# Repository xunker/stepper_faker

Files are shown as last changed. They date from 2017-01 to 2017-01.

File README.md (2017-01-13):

Stepper-Faker
=============

Arduino-based converter that lets unipolar steppers (e.g. 28BYJ-48 w/ ULN2003A)
pretend to be bipolar steppers for things like GRBL or Marlin. Built to work
with any Arduino-compatible atmega168/atmega328 board (ex: Arduino Uno or
Adafruit Pro Trinket). Also includes schematic for a custom carrier board that
makes connecting the steppers a snap!

Provides interface pins that work the same as the
[EasyDriver](http://www.schmalzhaus.com/EasyDriver/)
or [DRV8825/A4988 StepStick](https://www.pololu.com/product/1182) and can be
directly connected to a micro-controller running GRBL using the
[standard wiring](https://github.com/gnea/grbl/wiki/Connecting-Grbl).

Up to 3 steppers can be driven from one atmega328. Can be 5V or 12v, because
the original driver (e.g. ULN2003A) is still used.

The code is easily portable to other AVRs. Requires compatibility with the
[PinChangeInterrupt](https://github.com/NicoHood/PinChangeInterrupt) library and
the [Stepper class](https://www.arduino.cc/en/Reference/Stepper) included with
the Arduino IDE. Also requires that the micro-controller have at least 6 digital
pins available for each stepper (2-in, 4-out).

Will automatically power-down steppers after they have been idle for a period of
time. Does not yet support the SLEEP or ENABLE pins, but the RESET pin can be
used to a similar same effect.

Does not support micro-stepping, but may in the future.

### Compiling

[Download the code as a zip file](https://github.com/xunker/stepper_faker/archive/master.zip)
or clone the repository. Open `stepper_faker.ino` in the Arduino IDE (version
1.6.x or higher, please) and send it to your device.

### Wiring

General wiring requirement: connect the ground from your controller running
Stepper-Faker to the ground on the primary micro-controller running your
grbl/marlin/etc software.

If your primary controller has enough power to run your Stepper-Faker board and
all the steppers and your steppers are 5v, feel free to use that; otherwise you
will need to power those separately using the appropriate power source.

#### Stepper-Faker to steppers

Connect the "IN1/2/3/4" pins for each Stepper (A, B, or C) to the IN1/2/3/4 pins
on the included ULN2003A driver board. *Remember* that Stepper-Faker already
reverses the IN2 and IN3 pins, so you don't need to.

If your Stepper-Faker controller has enough power for all your steppers and they
are 5v, feel free to use that; otherwise you will need to power those separately
using the appropriate power source.

#### Stepper-Faker to GRBL

Follow the same [wiring directions as with EasyDriver](https://github.com/gnea/grbl/wiki/Connecting-Grbl#method-one-easydriver-v44).

#### Stepper-Faker as EasyDriver

Leave SLP, ENABLE, and RESET un-connected. Connect the the appropriate STEP and
DIR pins on your Stepper-Faker controller to the correct pins on your primary
controller running your software.

#### Stepper-Faker as DRV8825/A4988 StepStick

Leave SLEEP and RESET un-connected. Connect the the appropriate STEP and
DIR pins on your Stepper-Faker controller to the correct pins on your primary
controller running your software.

### Changes

Jan 13, 2016 - Add readme, update pins.

Jan 12, 2016 - Initial Commit

### To-Do

In no particular order.

* Remove BREADBOARDED_328 references in code.
* Set IN2/IN3 swapping with a #define.
* Set STEP and DIR pull-up or -down with #define.
* Set STEP and DIR high/low behaviour with a #define.
* Separate sleep timers per stepper.
* Ability to disable sleep timer.
* Add custom board files.
* Add Fritzing wiring diagrams.
* Conditionally [en/dis]able Serial, allow those pins to be used as SLEEP and ENABLE.
* Include support for [MiniCore](https://github.com/MCUdude/MiniCore), allow xtal pins to be used as SLEEP and ENABLE.
* PWM-based micro-stepping? Is it even worth it?
* Test with atmega32u4 for Arduino Micro/Leonardo.
* Test with attiny84.
* Test with attiny4313.
* Test with attiny1634.
* Support attiny85? Not enough pins. Analog hack on RESET, or share STEP/DIR using analogRead? Can't use interrupts then.

### License

GNU GPLv3

### Source and Author

Source code: https://github.com/xunker/stepper_faker

(C) 2017 Matthew Nielsen, xunker@pyxidis.org

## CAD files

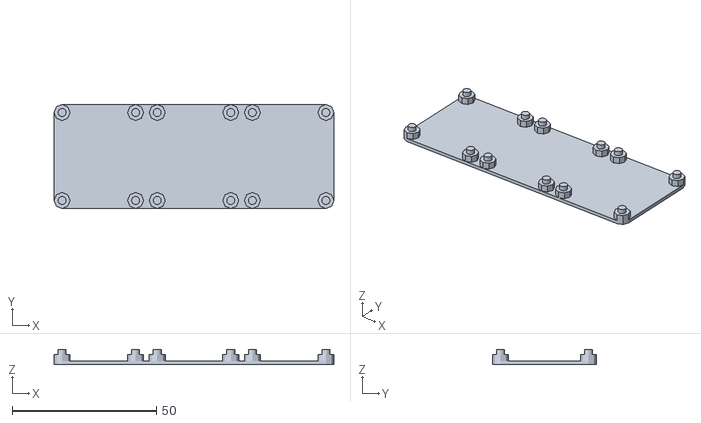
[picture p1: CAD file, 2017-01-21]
mount.stl
97.1 x 36.1 x 5.10

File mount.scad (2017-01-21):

/*
  Mount for uln2003A driver boards, common with 28BYJ-48 stepper motors.
*/

driver_board_hole_d = 2.8;
driver_board_standoff_d = driver_board_hole_d*2;
driver_board_standoff_h = 2.30; // how high the board should be off the bottom
driver_board_w = 31.0; // how much larger than board dimensions to make the base; //31.68 actually
driver_board_l = 36; // 35.2, actually
driver_board_thickness = 1.6; // 1.51 actually

// Thickness of bottom. Makes sense to be a multiple of your layer height.
floor_thickness = 1.2;

// Spacing between holes on X/Y planes
driver_board_hole_x_spacing = 25.5;
driver_board_hole_y_spacing = 30.5;

boards = 3; // number of boards to fit
board_spacing = 2; // spacing between boards, if multiple


module standoffs() {
  module standoff() {
    cylinder(d=driver_board_standoff_d, h=driver_board_standoff_h, $fn=8);
    translate([0,0,driver_board_standoff_h]) cylinder(d=driver_board_hole_d, h=driver_board_thickness, $fn=16);
  }

  translate([0,0,floor_thickness]) {
    translate([0, 0, 0]) standoff();
    translate([driver_board_hole_x_spacing, 0, 0]) standoff();
    translate([0, driver_board_hole_y_spacing, 0]) standoff();
    translate([driver_board_hole_x_spacing, driver_board_hole_y_spacing, 0]) standoff();
  }
}

module floor() {

  module floor_corner() {
    cylinder(d=driver_board_standoff_d, h=floor_thickness, $fn=8);
  }

  hull() {
    translate([0, 0, 0]) floor_corner();
    translate([driver_board_hole_x_spacing, 0, 0]) floor_corner();
    translate([0, driver_board_hole_y_spacing, 0]) floor_corner();
    translate([driver_board_hole_x_spacing, driver_board_hole_y_spacing, 0]) floor_corner();
  }
}

hull() {
  for (f = [0:boards-1]) {
    translate([(driver_board_w*f)+(board_spacing*f), 0, 0]) floor();
  }
}

for (f = [0:boards-1]) {
  translate([(driver_board_w*f)+(board_spacing*f), 0, 0]) standoffs();
}

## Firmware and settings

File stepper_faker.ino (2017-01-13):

/*

Translate bipolar stepper commands to unipolar stepper board, like ULN2003.

On an atmega328 with three axis, all pins except serial TX and RX are are used
(including LED_BUILTIN).

Microstepping, enable and sleep are currently not supported because we're out
of pins.


Atmega328 pins

RESET           1     (19/A5) 28  Stepper A IN4
RXD             2     (18/A4) 27  Stepper A IN3
TXD             3     (17/A3) 26  Stepper A IN2
Stepper A Dir   4 (2) (16/A2) 25  Stepper A IN1
Stepper B Dir   5 (3) (15/A1) 24  Stepper B IN4
Stepper C Dir   6 (4) (14/A0) 23  Stepper B IN3
VCC             7             22  GND
GND             8             21  AREF
OSC1            9             20  VCC
OSC2            10       (13) 19  Stepper B IN2
Stepper A Step  11 (5)   (12) 18  Stepper B IN1
Stepper B Step  12 (6)   (11) 17  Stepper C IN4
Stepper C Step  13 (7)   (10) 16  Stepper C IN3
Stepper C IN1   14 (8)   (9)  15  Stepper C IN2

GRBL settings that work for me. My set-up is 5V 28BYJ-48 steppers, ULN2003A
drivers, atmega328 running at 1mhz (internal):

Common to set-ups using above hardware:

$0=200    Step pulse, microseconds
$1=25     Step idle delay, msec

Things specific to my machine using ~6mm diameter shaft spools, losely based on
https://github.com/dherrendoerfer/uCNC_controller/tree/master/Extras/Plotter_v3:

$20=1     Enable soft limits.
$21=0     Disable hard limits.
$22=1     Enable homing cycle.
$23=3     Homing dir invert mask.
$27=2     Homing pull-off.
$32=1     Enable laser mode. $22 must be enabled for this to be enabled.
$100=92   X steps/mm.
$101=92   Y steps/mm.
$102=2500 Z steps/mm.
$110=250  X max rate, mm/min. Can be up to 350 with cooling. Based on $100.
$111=250  Y max rate, mm/min. Can be up to 350 with cooling. Based on $101.
$112=3    Z max rate, mm/min. Can be up to 5 with cooling. Based on $102.
$130=124  X max travel with something on the build plate. 153.5 when empty.
$131=68   Y max travel.
$132=22   Z max travel.

*/

#include <Stepper.h>
#include <PinChangeInterrupt.h>

/* Uncomment _one_ of the ones below to set the pin layout. BREADBOARDED_328
   divides the trigger pins between ports with theoretically will give slightly
   better preformance (but shouldn't make too much of a difference in real use.
   ADAPTER_328 groups the DIR and STEP pins together on sequential pins.
*/
// #define BREADBOARDED_328
#define ADAPTER_328

#define NUMBER_OF_STEPPERS 3
// There's no STEPPER_A define because it's assumed you'll have at leas one stepper
#define STEPPER_B // enable if NUMBER_OF_STEPPERS >= 2
#define STEPPER_C // enable if NUMBER_OF_STEPPERS >= 3

// Input pins
// Pull direction pin low to move "forward"
#ifdef ADAPTER_328
  #define STEPPER_A_DIR_PIN 2
#else
  #define STEPPER_A_DIR_PIN 2
#endif

#ifdef STEPPER_B
  #ifdef ADAPTER_328
    #define STEPPER_B_DIR_PIN 3
  #else
    #define STEPPER_B_DIR_PIN 8
  #endif
#endif

#ifdef STEPPER_C
  #ifdef ADAPTER_328
    #define STEPPER_C_DIR_PIN 4
  #else
    #define STEPPER_C_DIR_PIN A0
  #endif
#endif

// steps triggered when pin goes low
#ifdef ADAPTER_328
  #define STEPPER_A_STEP_PIN 5
#else
  #define STEPPER_A_STEP_PIN 3
#endif

#ifdef STEPPER_B
  #ifdef ADAPTER_328
    #define STEPPER_B_STEP_PIN 6
  #else
    #define STEPPER_B_STEP_PIN 9
  #endif
#endif

#ifdef STEPPER_C
  #ifdef ADAPTER_328
    #define STEPPER_C_STEP_PIN 7
  #else
    #define STEPPER_C_STEP_PIN A1
  #endif
#endif

/* Stepper library initialization */
/* STEPS_PER_REVOLUTION not technically needed since we're only moving one step at a time */
#define STEPS_PER_REVOLUTION 200

#ifdef ADAPTER_328
  Stepper stepperA(STEPS_PER_REVOLUTION, A2, A4, A3, A5);
#else
  Stepper stepperA(STEPS_PER_REVOLUTION, 4, 6, 5, 7);
#endif

#ifdef STEPPER_B
  #ifdef ADAPTER_328
    Stepper stepperB(STEPS_PER_REVOLUTION, 12, A0, 13, A1);
  #else
    Stepper stepperB(STEPS_PER_REVOLUTION, 10, 12, 11, 13);
  #endif
#endif

#ifdef STEPPER_C
  #ifdef ADAPTER_328
    Stepper stepperC(STEPS_PER_REVOLUTION, 8, 10, 9, 11);
  #else
    Stepper stepperC(STEPS_PER_REVOLUTION, A2, A4, A3, A5);
  #endif
#endif

// Used just for powering the steppers down when not in use
#ifdef ADAPTER_328
  const byte allStepperPins[] = {
    A2, A3, A4, A5,
  #ifdef STEPPER_B
    12, 13, A0, A1,
  #endif
  #ifdef STEPPER_C
    8, 9, 10, 11,
  #endif
  };
#else
  const byte allStepperPins[] = {
    4, 5, 6, 7,
  #ifdef STEPPER_B
    10, 11, 12, 13,
  #endif
  #ifdef STEPPER_C
    A2, A3, A4, A5,
  #endif
  };
#endif

Stepper* steppers[NUMBER_OF_STEPPERS] = {
  &stepperA,
#ifdef STEPPER_B
  &stepperB,
#endif
#ifdef STEPPER_C
  &stepperC,
#endif
};

const byte directionPins[NUMBER_OF_STEPPERS] = {
  STEPPER_A_DIR_PIN,
#ifdef STEPPER_B
  STEPPER_B_DIR_PIN,
#endif
#ifdef STEPPER_C
  STEPPER_C_DIR_PIN
#endif
};

const byte stepPins[NUMBER_OF_STEPPERS] = {
  STEPPER_A_STEP_PIN,
#ifdef STEPPER_B
  STEPPER_B_STEP_PIN,
#endif
#ifdef STEPPER_C
  STEPPER_C_STEP_PIN
#endif
};

// http://masteringarduino.blogspot.com/2013/10/fastest-and-smallest-digitalread-and.html
#define portOfPin(P)\
  (((P)>=0&&(P)<8)?&PORTD:(((P)>7&&(P)<14)?&PORTB:&PORTC))
#define ddrOfPin(P)\
  (((P)>=0&&(P)<8)?&DDRD:(((P)>7&&(P)<14)?&DDRB:&DDRC))
#define pinOfPin(P)\
  (((P)>=0&&(P)<8)?&PIND:(((P)>7&&(P)<14)?&PINB:&PINC))
#define pinIndex(P)((uint8_t)(P>13?P-14:P&7))
#define pinMask(P)((uint8_t)(1<<pinIndex(P)))

#define pinAsInput(P) *(ddrOfPin(P))&=~pinMask(P)
#define pinAsInputPullUp(P) *(ddrOfPin(P))&=~pinMask(P);digitalHigh(P)
#define pinAsOutput(P) *(ddrOfPin(P))|=pinMask(P)
#define digitalLow(P) *(portOfPin(P))&=~pinMask(P)
#define digitalHigh(P) *(portOfPin(P))|=pinMask(P)
#define isHigh(P)((*(pinOfPin(P))& pinMask(P))>0)
#define isLow(P)((*(pinOfPin(P))& pinMask(P))==0)
#define digitalState(P)((uint8_t)isHigh(P))

volatile signed int stepQueue[NUMBER_OF_STEPPERS];

boolean steppersPoweredDown = false;
unsigned int powerDownCounter = 0;
/* in cycles of loop(). On 1mhz atmega328 it's about 12 seconds. */
#define CHECK_FOR_POWER_DOWN_COUNTER_LIMIT 65534

void setup() {
  for(byte stepperNumber = 0; stepperNumber < NUMBER_OF_STEPPERS; stepperNumber++){
    pinMode(directionPins[stepperNumber], INPUT_PULLUP);
    pinMode(stepPins[stepperNumber], INPUT_PULLUP);

    /* 400 is good speed for 28byj steppers on uln2003 */
    steppers[stepperNumber]->setSpeed(400);

    stepQueue[stepperNumber] = 0;
  }

  attachPCINT(digitalPinToPCINT(STEPPER_A_STEP_PIN), readStepperA, FALLING);
  #ifdef STEPPER_B
    attachPCINT(digitalPinToPCINT(STEPPER_B_STEP_PIN), readStepperB, FALLING);
  #endif
  #ifdef STEPPER_C
    attachPCINT(digitalPinToPCINT(STEPPER_C_STEP_PIN), readStepperC, FALLING);
  #endif
}

void loop() {
  for(byte stepperNumber = 0; stepperNumber < NUMBER_OF_STEPPERS; stepperNumber++){
    if (stepQueue[stepperNumber] > 0) {
      powerDownCounter=0;
      steppers[stepperNumber]->step(1);
      stepQueue[stepperNumber]--;
    }

    if (stepQueue[stepperNumber] < 0) {
      powerDownCounter=0;
      steppers[stepperNumber]->step(-1);
      stepQueue[stepperNumber]++;
    }
  }

  if (powerDownCounter == 0) {
    steppersPoweredDown = false;
  }

  if (!steppersPoweredDown) {
    powerDownCounter++;

    if (powerDownCounter >= CHECK_FOR_POWER_DOWN_COUNTER_LIMIT) {
      powerDownSteppers();
    }
  }
}

void powerDownSteppers() {
  if (steppersPoweredDown)
    return;
  steppersPoweredDown = true;
  for(byte i = 0; i < sizeof(allStepperPins); i++){
    digitalLow(allStepperPins[i]);
  }
}

void readStepperA() {
  if (isLow(directionPins[0])) {
    stepQueue[0]++;
  } else {
    stepQueue[0]--;
  }
}

#ifdef STEPPER_B
  void readStepperB() {
    if (isLow(directionPins[1])) {
      stepQueue[1]++;
    } else {
      stepQueue[1]--;
    }
  }
#endif

#ifdef STEPPER_C
  void readStepperC() {
    if (isLow(directionPins[2])) {
      stepQueue[2]++;
    } else {
      stepQueue[2]--;
    }
  }
#endif
